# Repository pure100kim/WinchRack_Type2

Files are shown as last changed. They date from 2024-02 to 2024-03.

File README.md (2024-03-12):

# WinchRack_Type2 

# 1. WinchRack_Type2_V1 Release

WinchRack_Type2 V1 for ERCF buffer 

youtube WinchRack_Type2 V1 Testing video : https://www.youtube.com/watch?v=6KahxyvfvtI<br>

ERCF(당근)과 연동하여 테스팅한 유투브 영상입니다.<br>
youtube WinchRack_Type2 V1 Applying ERCF video : https://www.youtube.com/watch?v=UDQim4SroeI

v6cl (방탄쪼끼) is a nice member of the same country and VORON User kakao chat room. <br>
He is adept at design and has helped shortcomings in the multi-color ERCF buffer, for which we are grateful. <br>
Building upon his design, I have received wonderful ideas to modify the structure for improved spatial aspects and easier spool install.

방탄쪼끼님 멋져요!

You can access his original material through the link below.<br>

v6cl WinchRack original Verison github : https://github.com/v6cl/WinchRack/tree/main

v6cl Test youtube video : https://www.youtube.com/shorts/trHfZH3sDRs

# WinchRack Type2

<div align="center">
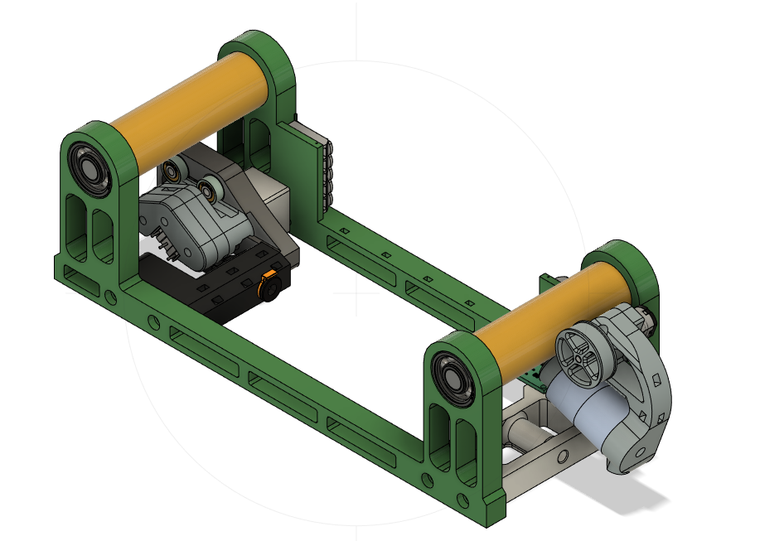
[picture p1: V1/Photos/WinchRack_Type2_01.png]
	<br>
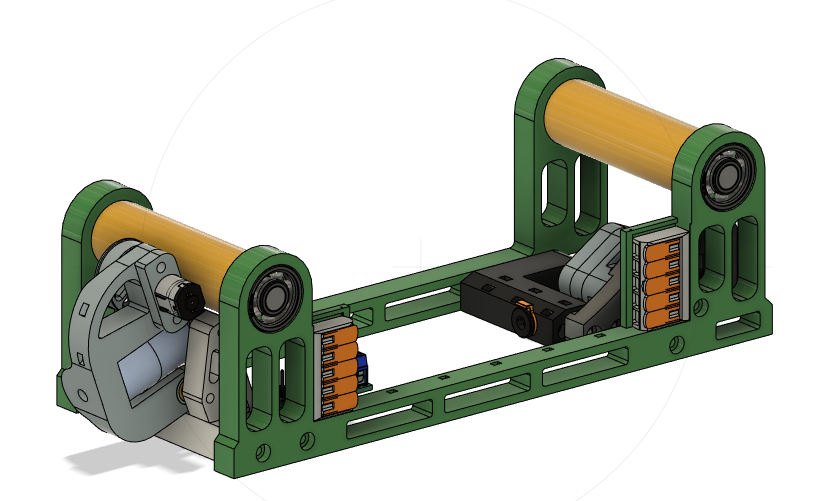
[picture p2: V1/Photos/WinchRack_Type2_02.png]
	<br>
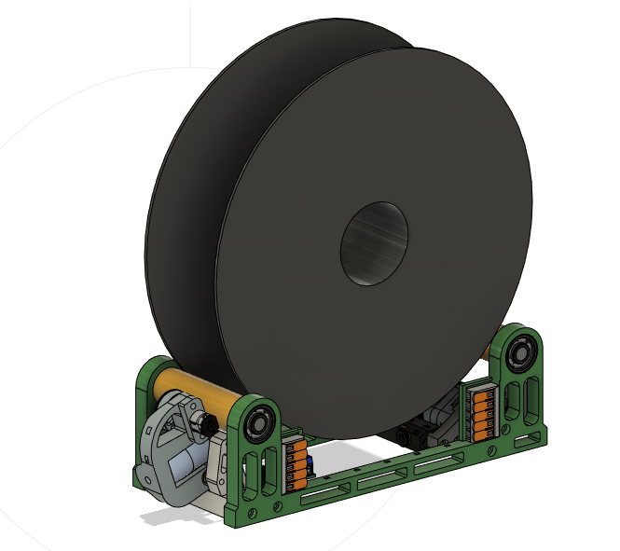
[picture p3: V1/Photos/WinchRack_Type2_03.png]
	<br>
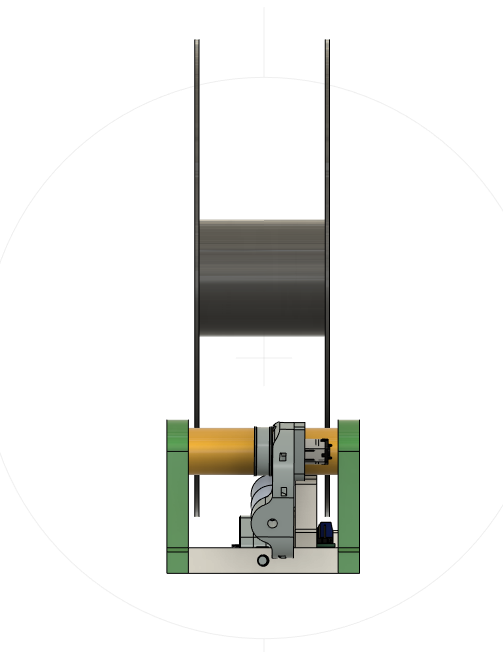
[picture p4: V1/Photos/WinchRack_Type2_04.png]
 	<br>
</div>
<br>

# BOM
Winchrack base component list has been imported as is.<br>

Wago 5pin x 2

(Choose option1) Opto endstop x 1 (https://zrr.kr/ZYrV)

(Choose option2) Opto interrupt x 1 (https://a.aliexpress.com/_oFFfkt0)

n20 gear motor 300 rpm 5v ~ 6v x 1 (https://zrr.kr/33Ta)

ls-p20/15 3kg x 2 (https://zrr.kr/Rqkb)

mosfet switch 1ch x 1 (https://zrr.kr/TrOc)

608zz x 8 (optoion 1 more : you can get 4mm bearing ball 608zz decomposition)

623zz x 8

silicon ring x 1 (https://zrr.kr/E5Dk)

PTFE tube 3x4 or 2x4

m3 insert nut (OD 5mm, L 4mm)

m3 bolts

m4 bolt 15mm x 2 (For ls-p20/15)

m2 self tapping screw 8~10mm x 4

6mm collet for 4mm PTFE Tube x 1 (https://zrr.kr/7WdG)

D2F Micro switch

4mm Bearing ball (608zz including 7 pcs 4mm ball. You can get it decomposition 608zz) 

<br>
<br>
<br>

# Connection Diagram (연결도)
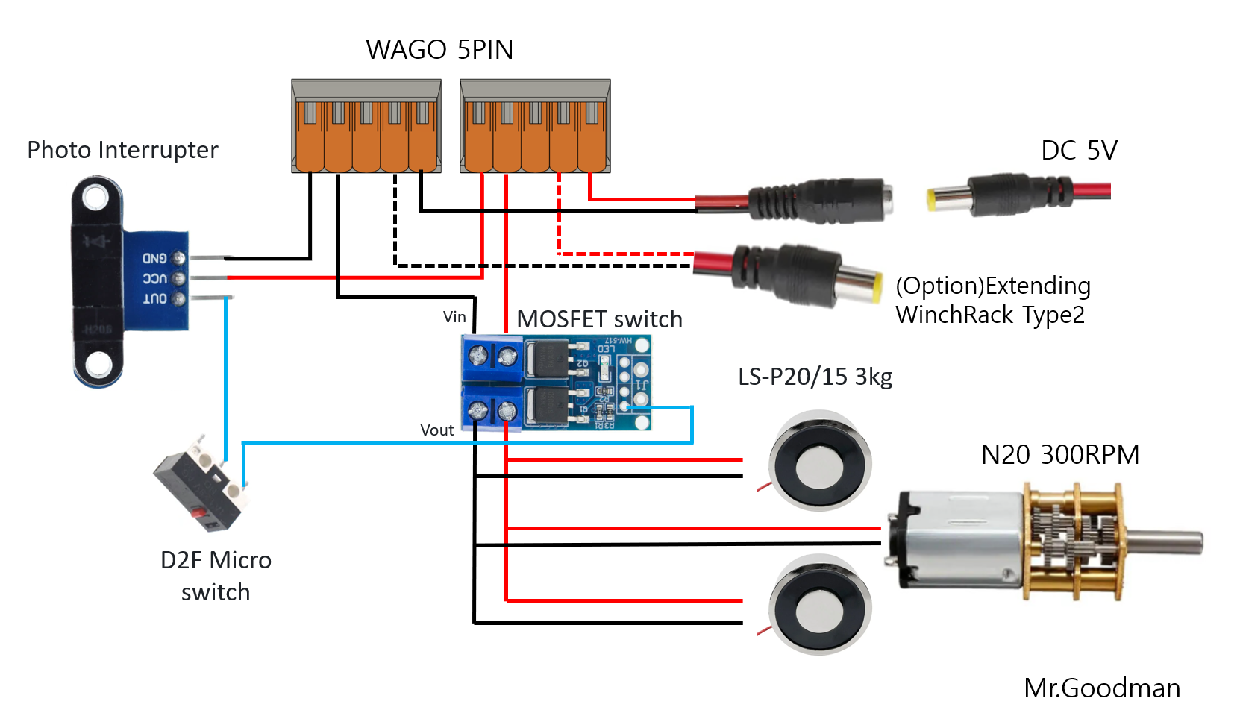
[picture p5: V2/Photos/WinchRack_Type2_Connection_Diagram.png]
<br>

<br>
<br>
<br>
# Assembly precautions
When assembling, make sure to clean the inside of the 608 bearing to ensure smooth rotation when turned.
The bearing should rotate smoothly with minimal friction, at least for several turns.

Due to the friction of the bearing balls, the front and rear rails move, so be sure to assemble the 4mm bearings and switches.
<br>
<br>

# Depend on AccelMotor Revers Assembly motor direction
It is permissible to change the polarity of the power supply to reverse the motor direction, or to relocate the motor while maintaining the polarity marked on the motor as positive (+).
If you changing motor location, use stl file AccelMotor_mag_holder_Frame_Reverse.stl and FrontFoot_Reverse.stl

<br>
<br>
<br>

# 2. WinchRack_Type2_V2 version Release

1. AccelPedal 623zz 고정할때 둥근머리 볼트로 고정해야 합니다.<br>
When fixing AccelPedal 623zz, you should use a rounded head M3 bolt.

2. AccelPedal 조립 후 스풀 롤러와 Accel Roller 고무와 마찰이 잘 되도록 하기 위해<br>
   전자석이 1mm 정도 떨어졌다 붙었다 하게 됩니다.<br>
   최적 위치 조절하면서 볼트를 조여 주세요.<br>
After assembling the AccelPedal, the electromagnet should be positioned about 1mm away and then attached,<br>
allowing for optimal adjustment while tightening the rear bolt to ensure good friction between the spool roller and the Accel Roller rubber.   

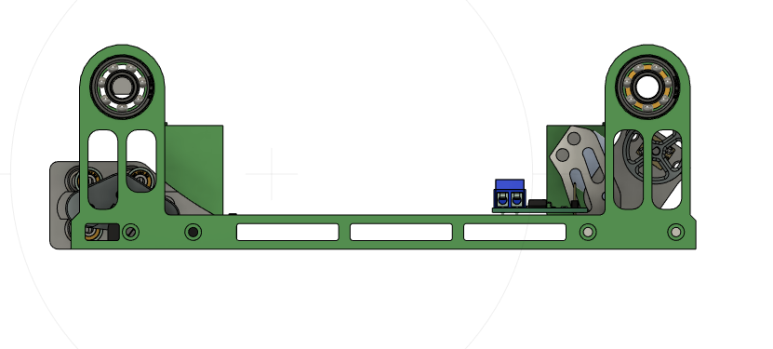
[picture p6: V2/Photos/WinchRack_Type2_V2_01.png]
<br>

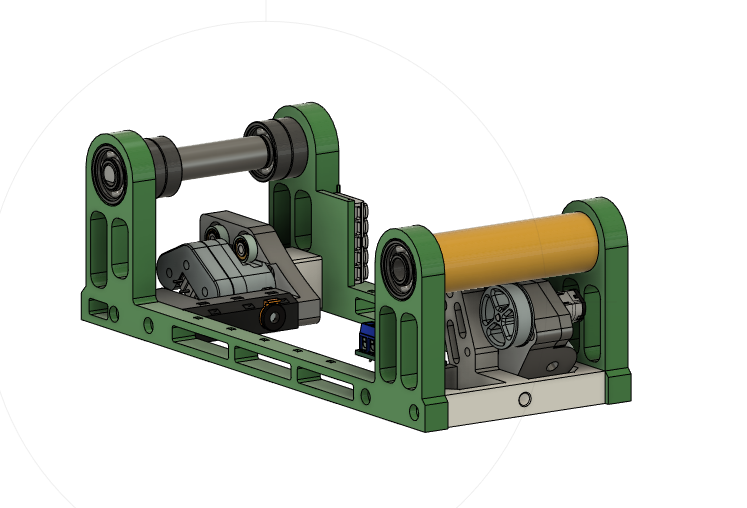
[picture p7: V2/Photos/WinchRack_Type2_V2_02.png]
<br>

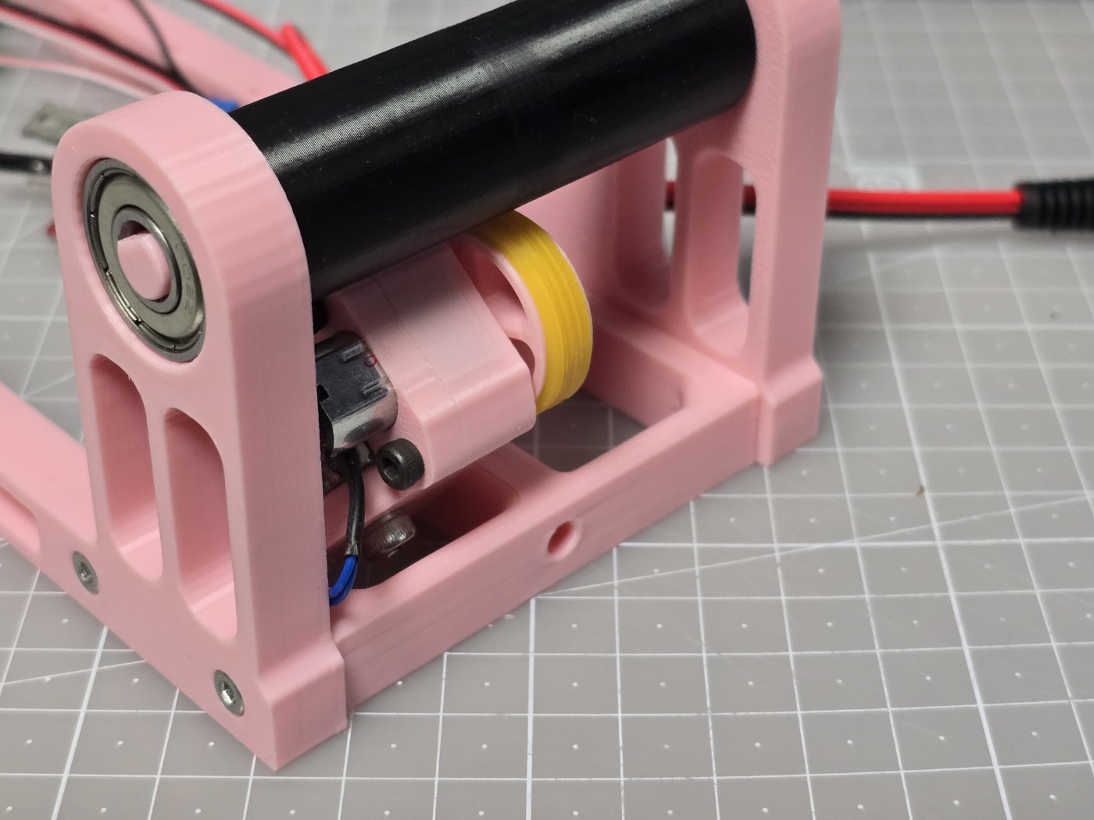
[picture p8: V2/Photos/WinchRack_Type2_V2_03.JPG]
<br>

<br>
<br>
<br>

# 3. WinchRack_Type2 Weight : Filament reamiining Weight version Release

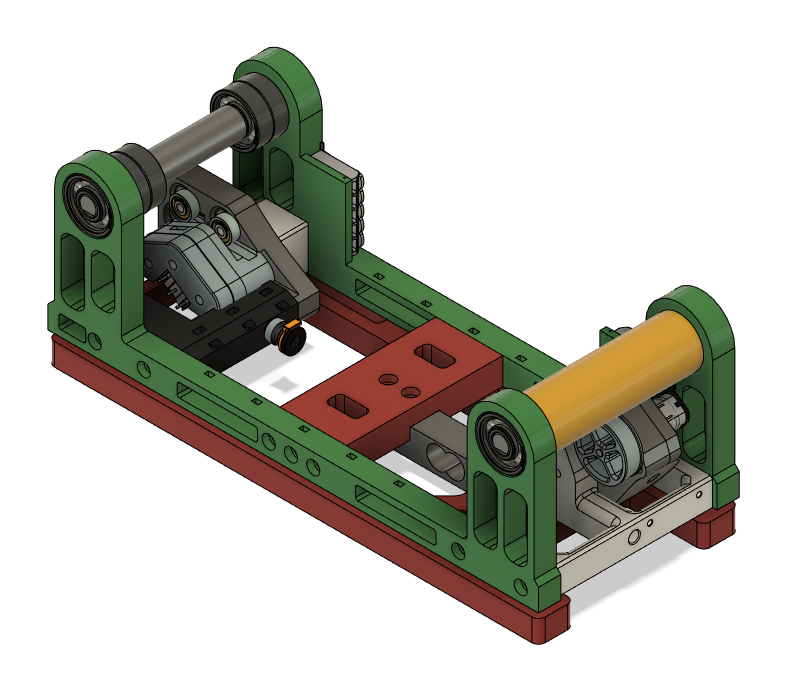
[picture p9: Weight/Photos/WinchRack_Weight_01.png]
<br>

# WinchRack_Type2 Weight Version Add Bom (추가 부품)

1. 5kg 무게 저울 센서 (보드 포함) 1개 <br>
   5kg Loadcell including HX711
2. 아두이노 NANO 1개 <br> 
   Arduino Nano Board <br>
   Recommnad small size board : ESP32-C3    
4. 0.96 inch OLED 12C 버전 1개 <br>
5. M3 insert 6 PCS <br>
6. M4*12mm 4 PCS <br>
7. M3*8mm 6개<br>
8. 기타 전원선<br>

<br>
<br>
<br>

# WinchRack Type2 V3 BelayStlye : Design in progress

<br>
<br>

# History <br>
### 21 Feb 2024 : Changing Modeling base on v6cl WinchdRack <br>
### 22 Feb 2024 : Currently in beta testing. <br>
### 23 Feb 2024
1. File modification for filament switch performance enhancement : SensorDetection_middle_Narrow.stl file.
2. Motor Mount location changing.
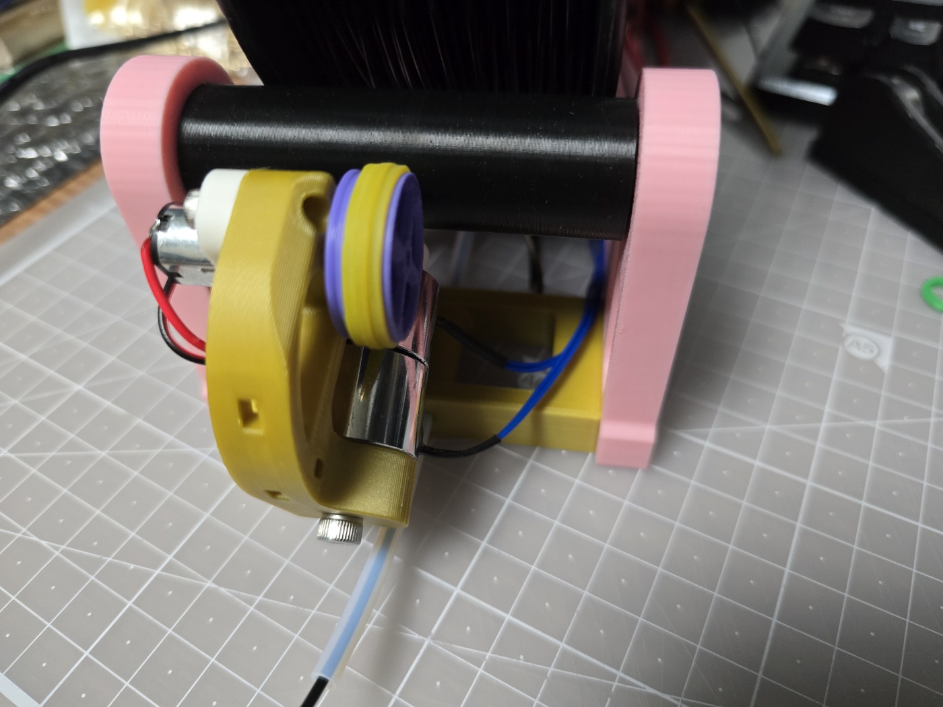
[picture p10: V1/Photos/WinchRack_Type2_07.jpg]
<br>

### 24 Feb 2024<br>
1. Changing Rear Roller 608zz 4pcs instead of printout TPU Roller.
2. Add 2.5mm ~ 3mm space and 41mm pipe. You can adjust gap.
3. Version1 Final Release
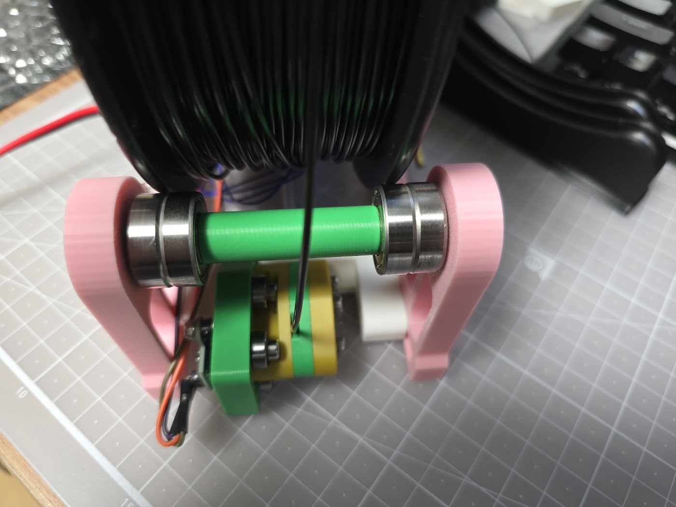
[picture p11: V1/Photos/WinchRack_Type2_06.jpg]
<br>

### 27 Feb 2024<br>
락액락 통에 넣을 수 있는 사이즈로 길이를 줄였습니다.<br>
1. Reduce lenth to 227mm
   
<br>

### 28 Feb 2024<br>
필라멘트 잔여량 측정이 가능하도록 무게 측정하는 버전 개발 진행<br>
1. Spool Weight Beta Testing version Modeling added

<br>

### 29 Feb 2024<br>
테스팅결과 스풀의 무게로 롤러 양쪽이 쳐지는 문제가 발생이 되었습니다.<br>
구조적으로 쳐짐이 발생되지 않도록 설계 보강하였습니다.<br>

1. Design Change to Withstand Spool Weight Load <br>
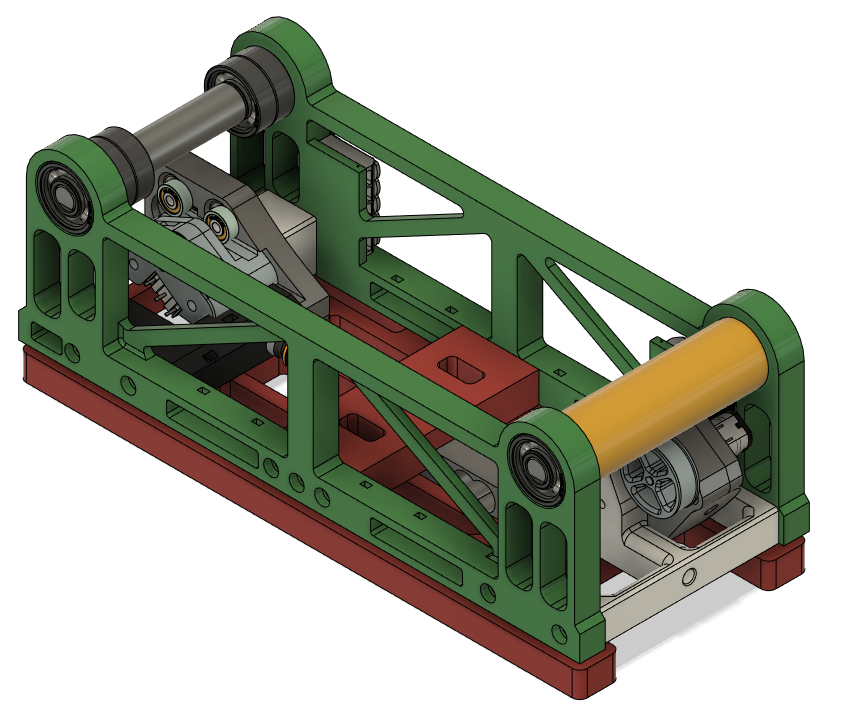
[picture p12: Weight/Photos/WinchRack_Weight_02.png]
<br>

### 01 Mar 2024<br>
1. Filament Remaing Weight arduino coding verify complted <br>
2. Relase Measure Filament remaing weight <br>
3. Writing Connection Diagram <br>
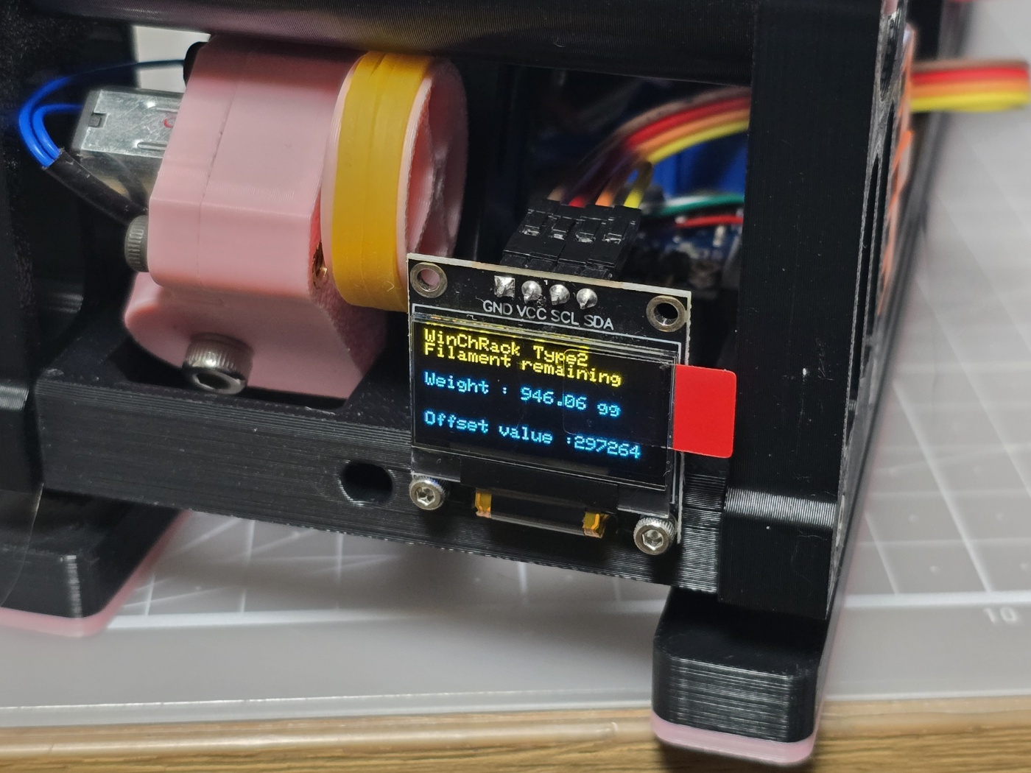
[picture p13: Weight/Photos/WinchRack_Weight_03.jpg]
<br>

### 12 Mar 2024<br>
1. WinchRack V3 is redesigning the sensor rail to be simpler and reduce bearing parts.

감사합니다.

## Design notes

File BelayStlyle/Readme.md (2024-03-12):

The design of the sensor rail method is being changed to another style.<br>
Many bearings will be removed.

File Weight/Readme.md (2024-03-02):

# WinchRack_Type2 V3 Weight scale Version Relase

Youtube video : https://youtu.be/h_89rF7SB6s?si=DVgz_AW4CbowRDjg

<br>

1. AccelPedal 623zz 고정할때 둥근머리 볼트로 고정해야 합니다.<br>
When fixing AccelPedal 623zz, you should use a rounded head M3 bolt.

2. AccelPedal 조립 후 스풀 롤러와 Accel Roller 고무와 마찰이 잘 되도록 하기 위해<br>
   전자석이 1mm 정도 떨어졌다 붙었다 하게 됩니다.<br>
   최적 위치 조절하면서 볼트를 조여 주세요.<br>
After assembling the AccelPedal, the electromagnet should be positioned about 1mm away and then attached,<br>
allowing for optimal adjustment while tightening the rear bolt to ensure good friction between the spool roller and the Accel Roller rubber.   

<br>

<br>

<br>

# Add Bom (추가 부품)

1. 5kg 무게 저울 센서 (보드 포함) 1개 <br>
   5kg Loadcell including HX711
2. 아두이노 NANO 1개 <br>
   Arduino Nano Board
3. 0.96 inch OLED 12C 버전 1개 <br>
4. M3 insert 6 PCS <br>
5. M4*12mm 4 PCS <br>
6. M3*8mm 6개<br>
7. M3*8mm 1개(둥근머리) <br>
8. 기타 전원선<br>

<br>

<br>

# Loadcell Connection Diagram
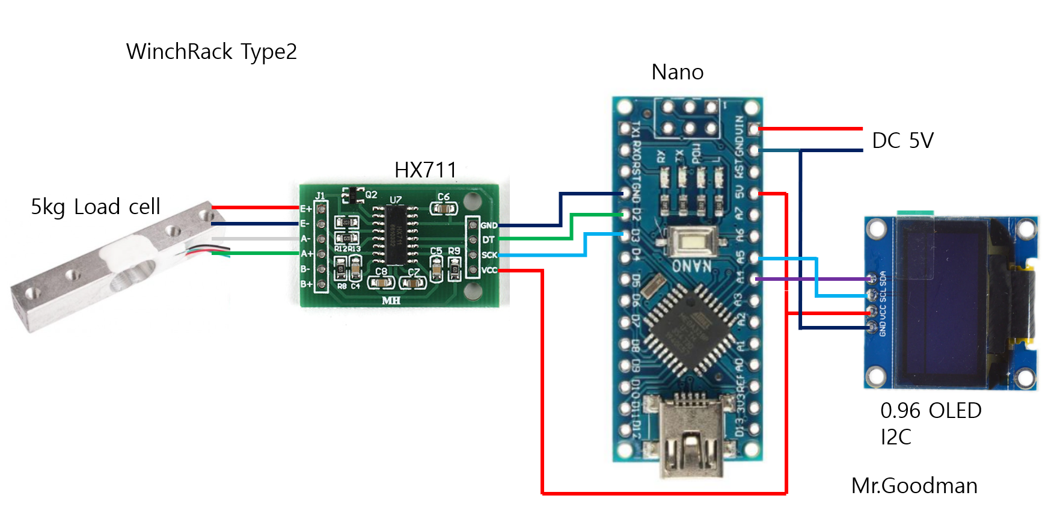
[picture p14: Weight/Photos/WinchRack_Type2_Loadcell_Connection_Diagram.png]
<br>

# History

29 Feb 2024 <br>
Design Change to Withstand Spool Weight Load <br>

01 Mar 2024
1. LoadCell Arduino Nano Coding complted <br>
2. Writging Connection Diagram <br>

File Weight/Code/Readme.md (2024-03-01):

아두이노로 필라멘트 잔량을 표기하는 아두이노 코드입니다.

# 적용 순서

1. WinchRack_offset_measure.ino 코드 적용 후 offset값 측정 및 기입 <br>
2. 빈 스풀 무게 실측값 측정<br>
3. WinchRack_Filament_remaining_Weight.ino 코드에 offset값과 빈스풀 무게 실측값 기입<br>
4. 코드 적용<br>

위에 1번과 2번에서 빈스풀을 올린 후 offset값을 측정하여도 무방하긴합니다.<br>
코드 약간 수정하면 되긴합니다.

감사합니다.

# Application Sequence

1. Apply the WinchRack_offset_measure.ino code and measure the offset value, then record it.  <br>
2. Measure the actual weight of the empty spool. <br>
3. Enter the offset value and the measured weight of the empty spool into the WinchRack_Filament_remaining_Weight.ino code. <br>
4. Apply the modified code. <br>

It is acceptable to measure the offset value after winding the empty spool in steps 1 and 2 above.
Minor modifications to the code may be necessary.

Thankyou~ :D

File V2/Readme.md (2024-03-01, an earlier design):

# WinchRack_Type2_V2

락앤락 통에 넣을 수 있도록 사이즈를 줄인 버전입니다.

전체 사이즈 : 가로 227mm x 폭 90mm x 높이 220mm (스풀 지름 200mm 일때 기준)

# Assembly precautions
When assembling, make sure to clean the inside of the 608 bearing to ensure smooth rotation when turned.
The bearing should rotate smoothly with minimal friction, at least for several turns.

Due to the friction of the bearing balls, the front and rear rails move, so be sure to assemble the 4mm bearings and switches.
<br>
<br>

1. AccelPedal 623zz 고정할때 둥근머리 볼트로 고정해야 합니다.<br>
When fixing AccelPedal 623zz, you should use a rounded head M3 bolt.

2. AccelPedal 조립 후 스풀 롤러와 Accel Roller 고무와 마찰이 잘 되도록 하기 위해<br>
   전자석이 1mm 정도 떨어졌다 붙었다 하게 됩니다.<br>
   최적 위치 조절하면서 볼트를 조여 주세요.<br>
After assembling the AccelPedal, the electromagnet should be positioned about 1mm away and then attached,<br>
allowing for optimal adjustment while tightening the rear bolt to ensure good friction between the spool roller and the Accel Roller rubber.

3. 만약 그래도 Accel Roller와 스풀 롤러간 마찰이 잘 안된다고 하면 스풀 롤러 지름 22mm에서 23mm로 CAD수정하여 출력해보세요.
   스풀 롤러는 외경 22mm, 내경 8mm, 길이 69mm 입니다.

<br>

<br>
<br>
<br>

둥근머리 M3*10mm로 먼저 조립한 후 전자석을 조립합니다.<br>

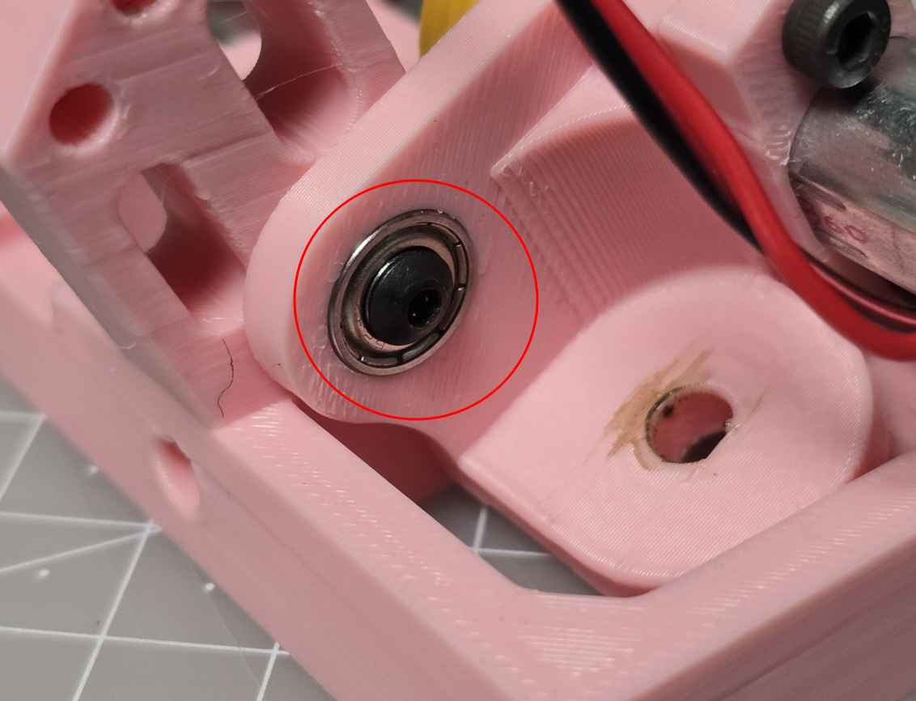
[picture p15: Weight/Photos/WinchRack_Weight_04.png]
<br>

<br>

<br>
<br>
<br>

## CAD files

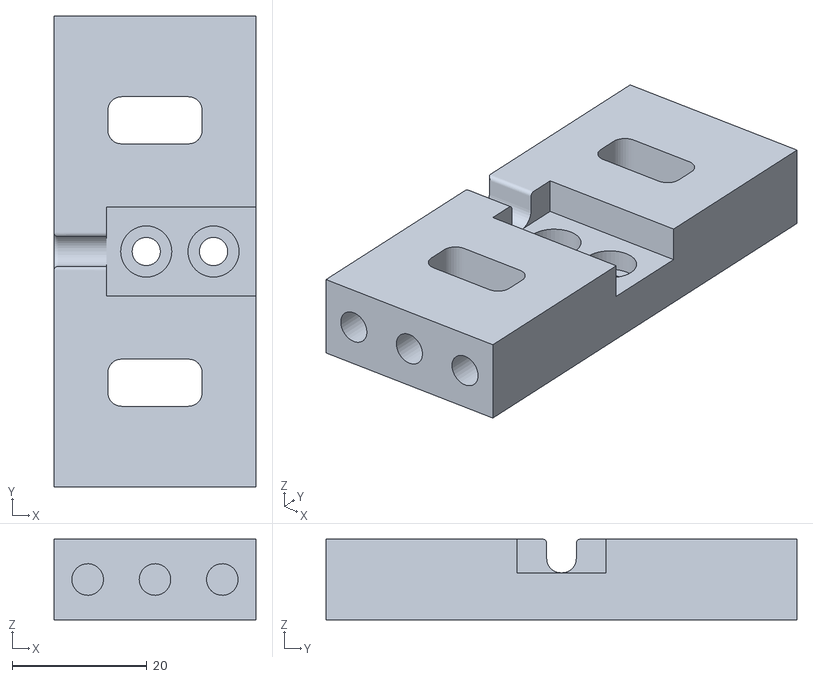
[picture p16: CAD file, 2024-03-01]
Weight/STLs/WeightBase/Weight_Holder.stl
30.0 x 70.0 x 12.0

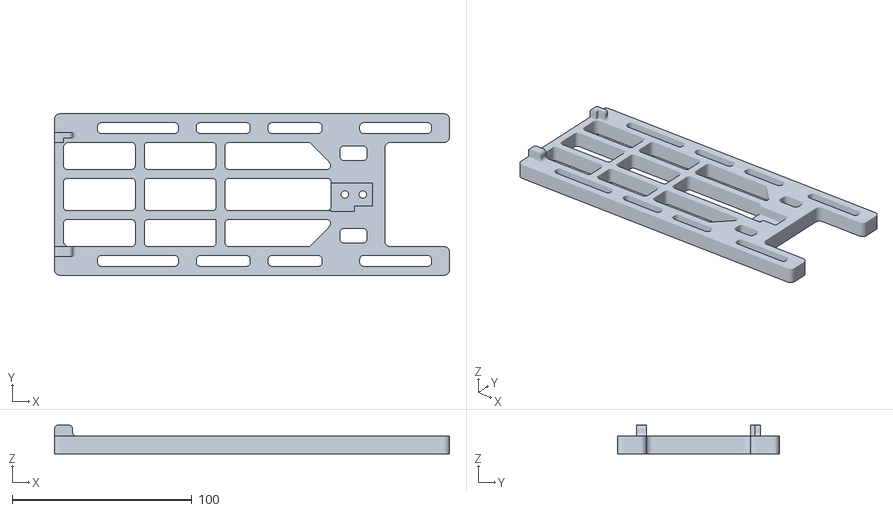
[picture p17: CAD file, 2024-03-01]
Weight/STLs/WeightBase/Weight_base.stl
220.0 x 90.0 x 16.0

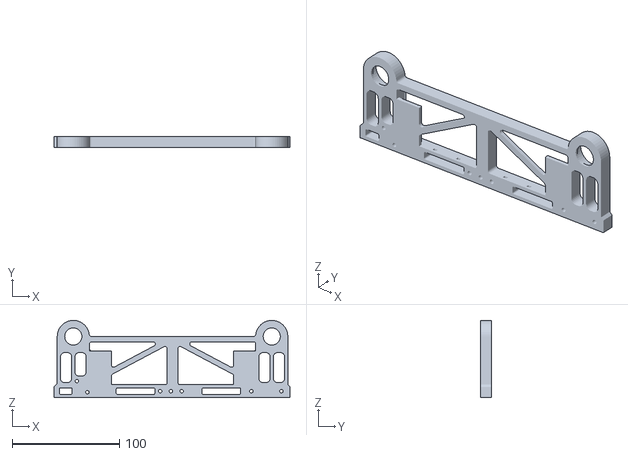
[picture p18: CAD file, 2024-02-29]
Weight/STLs/WeightBase/Base_Right_Weight.stl
220.0 x 10.0 x 72.0

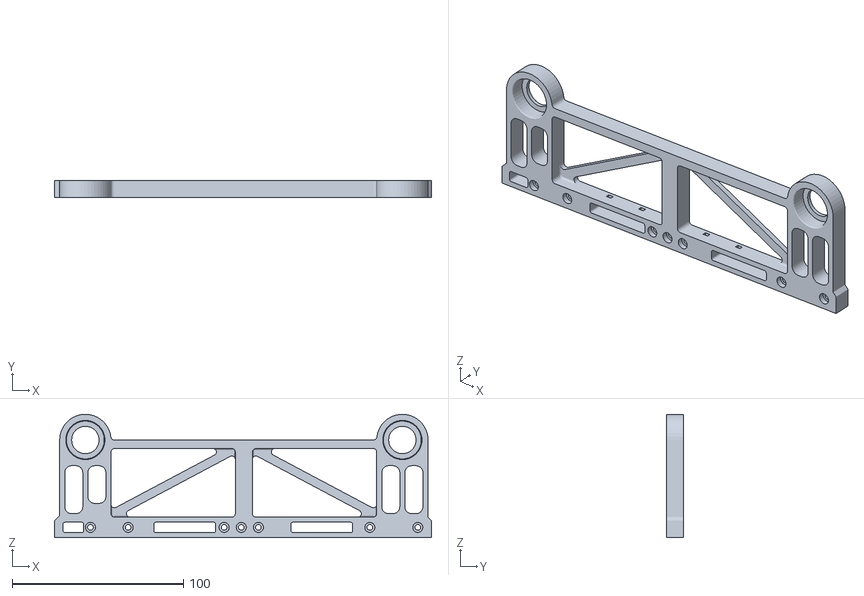
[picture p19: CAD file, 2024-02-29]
Weight/STLs/WeightBase/Base_Left_Weight.stl
220.0 x 10.0 x 72.0

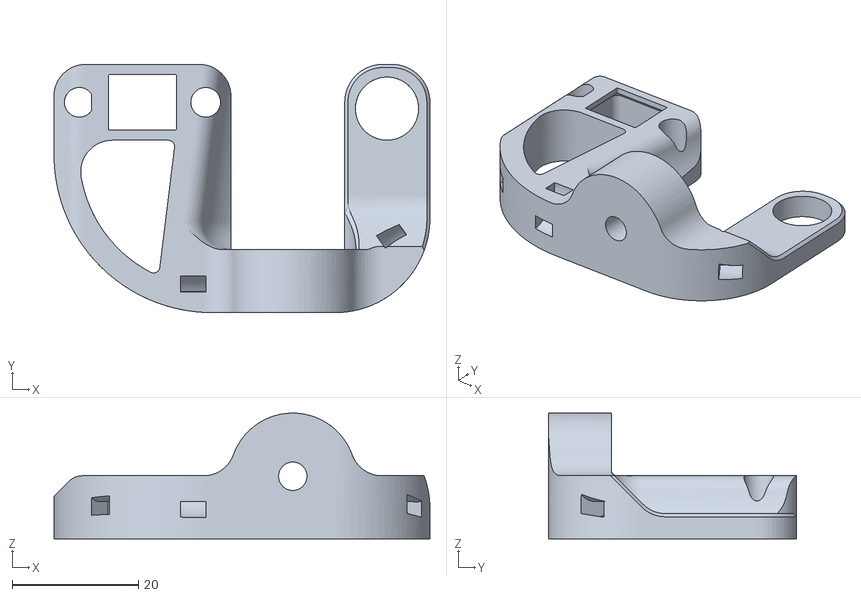
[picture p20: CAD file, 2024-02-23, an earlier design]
V1/STLs/AccelMotor/AccelMotor_mag_holder_Frame_Reverse.stl
59.5 x 39.3 x 19.9

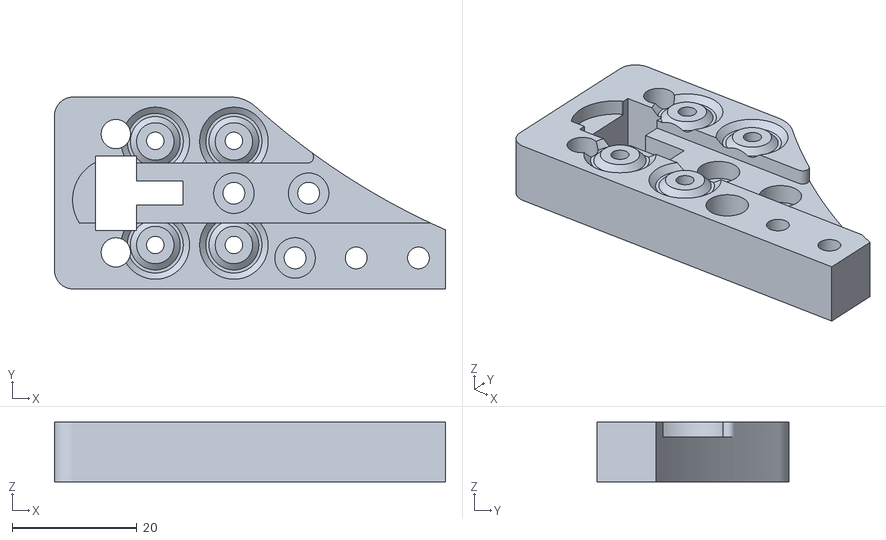
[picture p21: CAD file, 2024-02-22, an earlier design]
V1/STLs/SensorDetection/BufferRail.stl
62.8 x 30.8 x 9.58

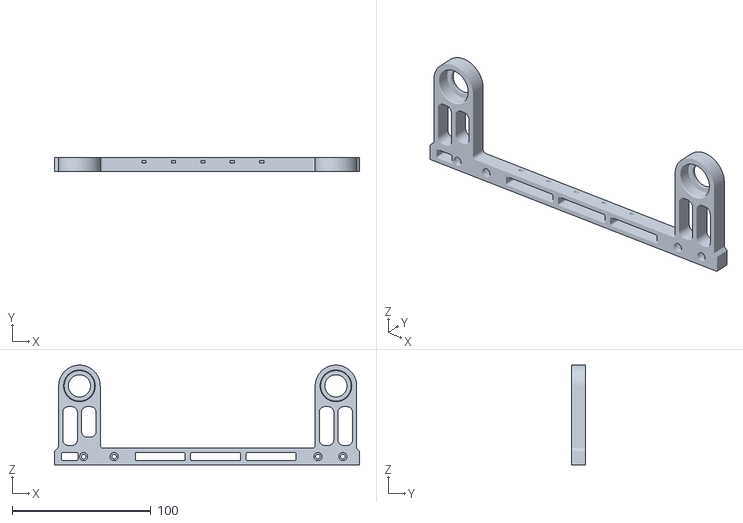
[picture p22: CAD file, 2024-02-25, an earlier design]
V1/STLs/SpoolBase/Base_Left.stl
220.0 x 10.0 x 72.0

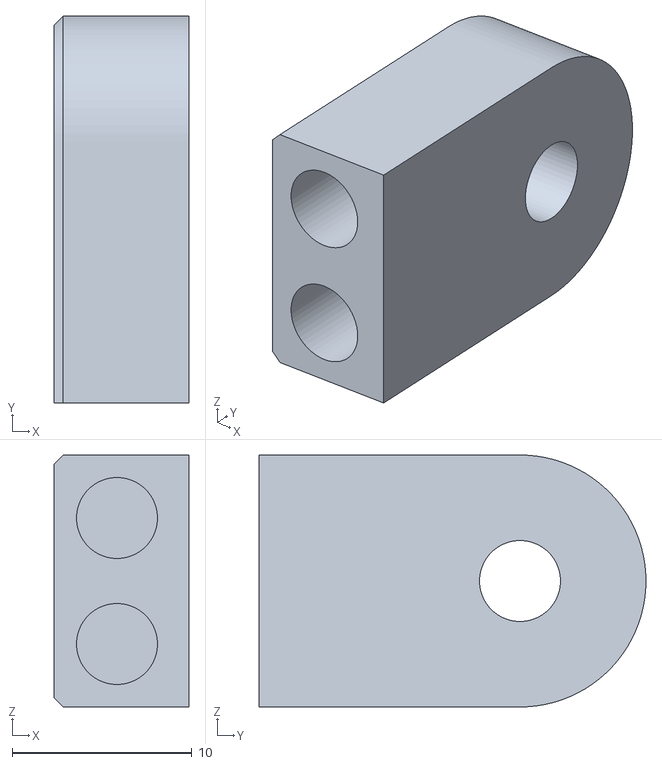
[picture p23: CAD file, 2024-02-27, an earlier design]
V2/STLs/AccelMotor/AccelPedal_mag_holder.stl
7.50 x 21.5 x 14.0

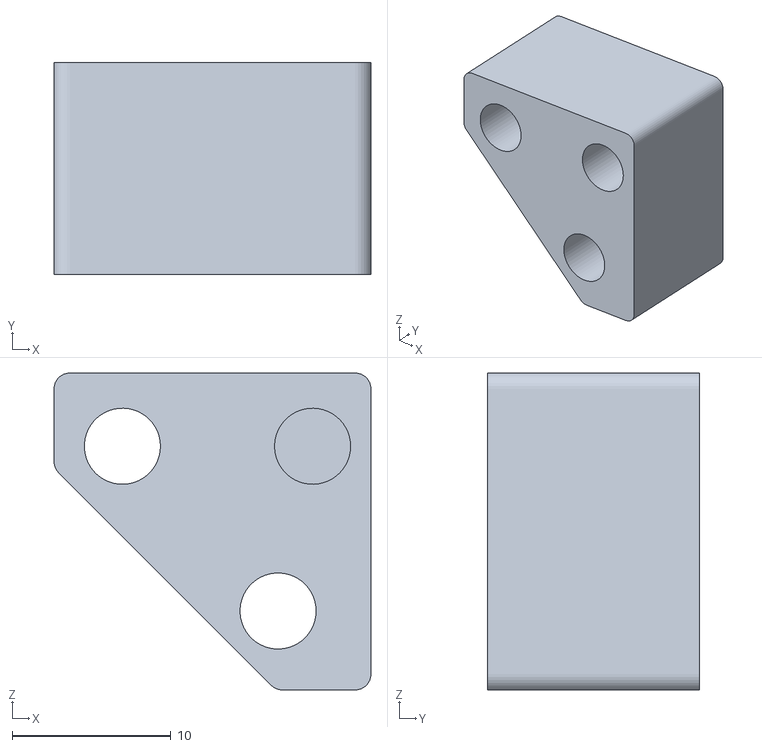
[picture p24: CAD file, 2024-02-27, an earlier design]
V2/STLs/SensorDetection/SensorDetection_sensor_basemount.stl
20.0 x 13.3 x 20.0

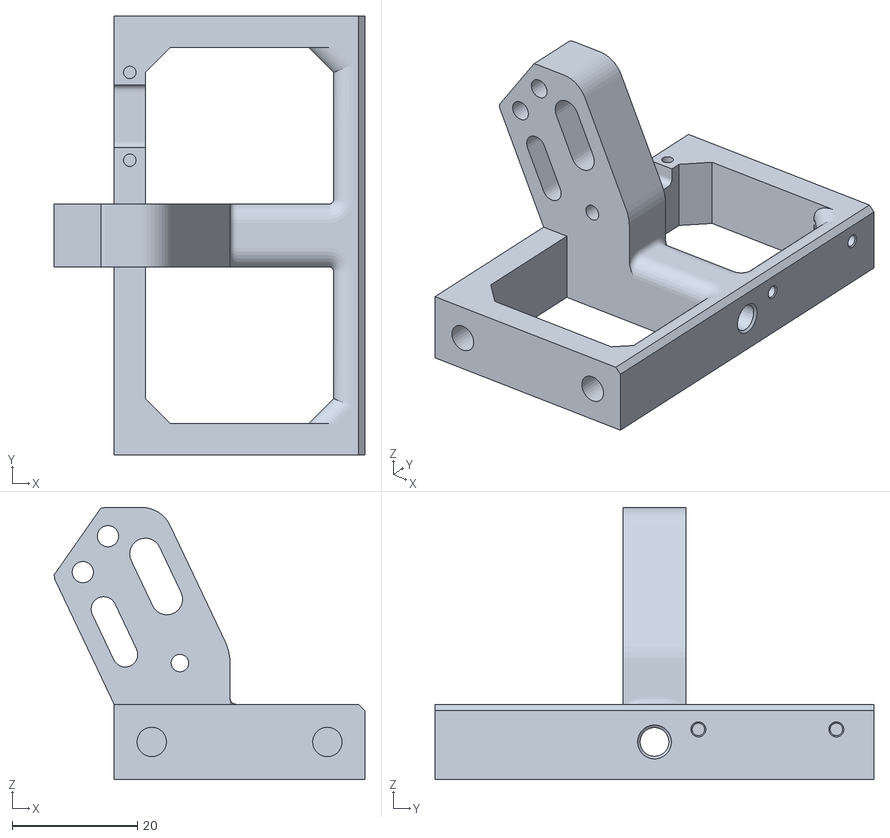
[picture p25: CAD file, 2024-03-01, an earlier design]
V2/STLs/SpoolBase/Front Base_Accel_Pedal_Mount.stl
49.6 x 70.0 x 43.4

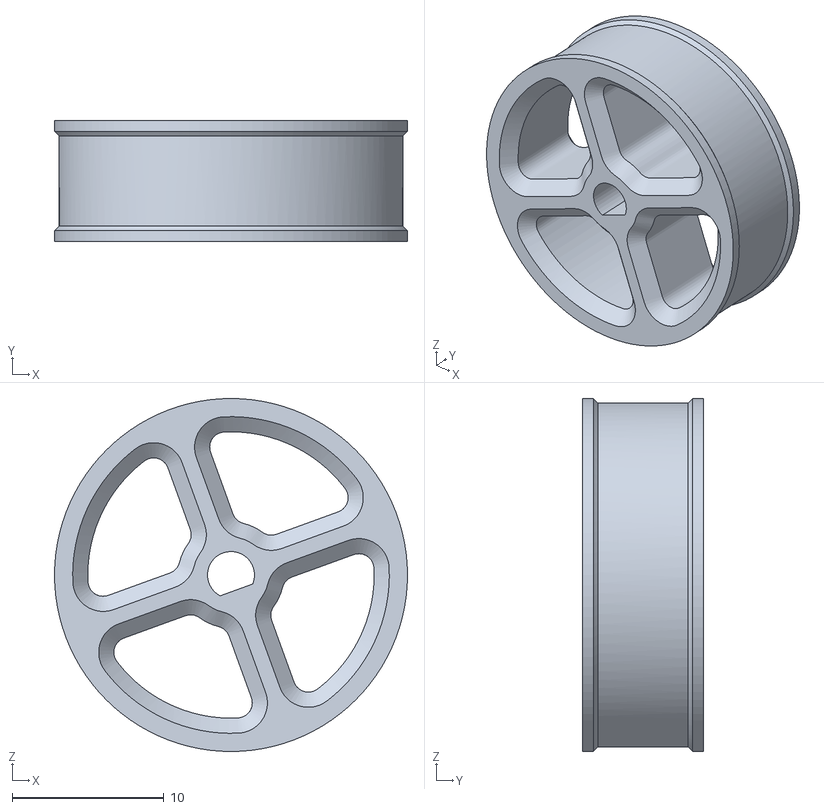
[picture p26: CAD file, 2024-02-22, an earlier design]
V1/STLs/AccelMotor/AccelMotor_mag_Roller.stl
23.3 x 8.00 x 23.3

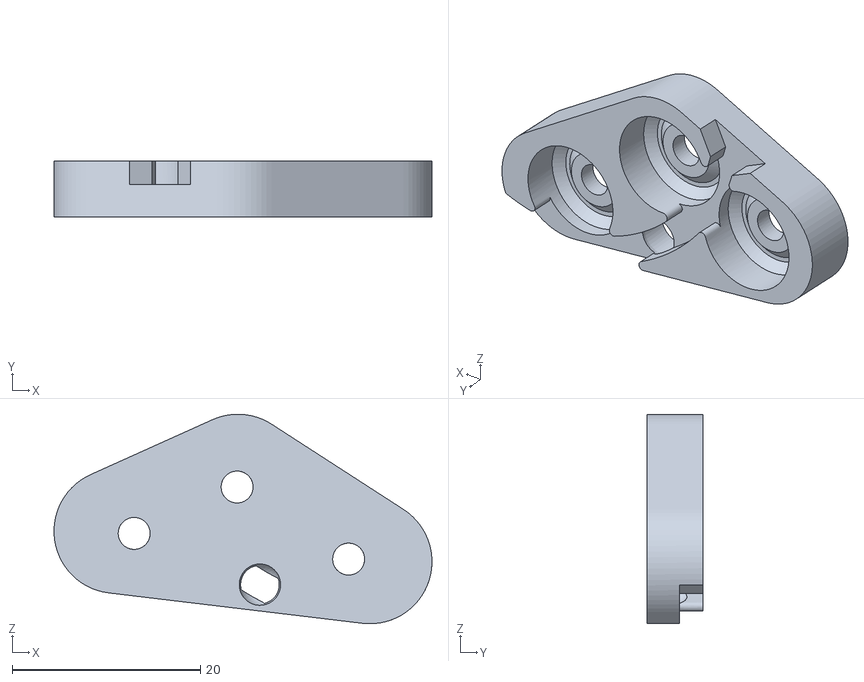
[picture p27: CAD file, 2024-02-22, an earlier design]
V1/STLs/SensorDetection/SensorDetection_middle.stl
40.2 x 5.91 x 22.3

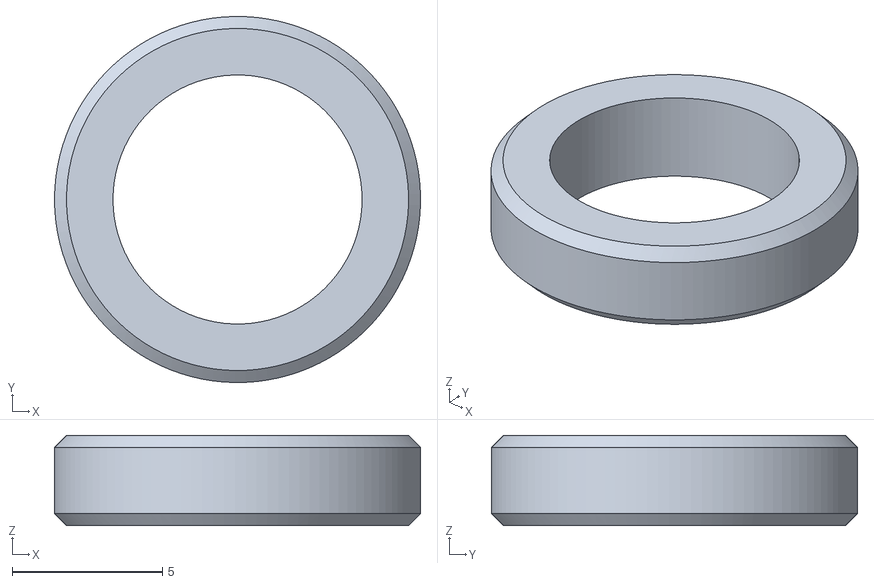
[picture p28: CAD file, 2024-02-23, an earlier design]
V1/STLs/SpoolBase/3mm_space.stl
12.2 x 12.2 x 3.00

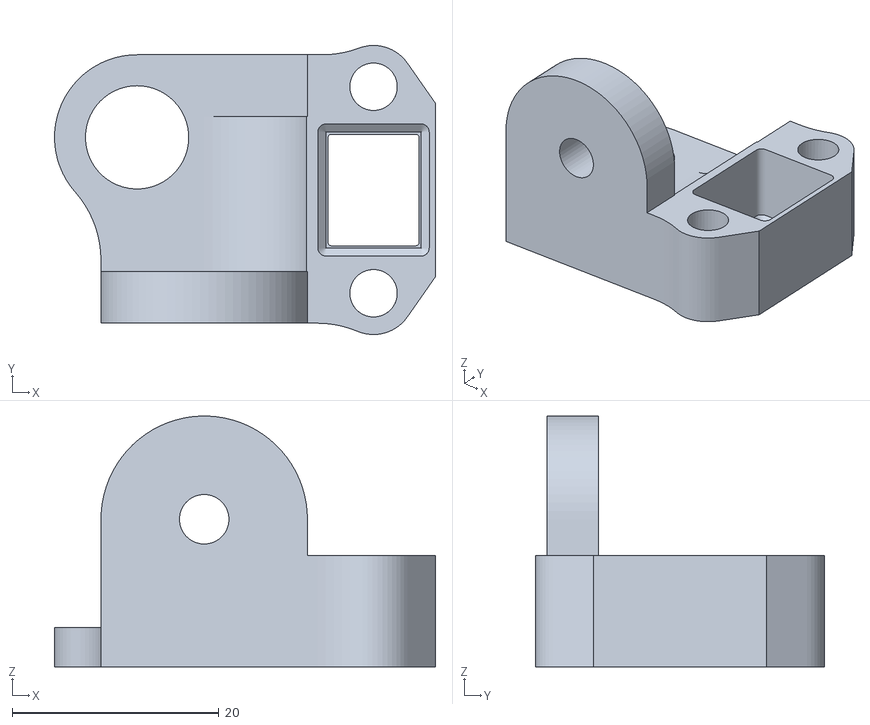
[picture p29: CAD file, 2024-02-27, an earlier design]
V2/STLs/AccelMotor/AccelPedal_mag_Body_Left.stl
36.9 x 28.0 x 24.3

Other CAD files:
V1/CAD/WinchRack_windre_Type2.step
V2/STLs/SensorDetection/SensorDetection_middle_Narrow.stl
V1/STLs/AccelMotor/AccelMotor_motor_holder.stl
V1/STLs/AccelMotor/AccelMotor_mag_holder.stl
V1/STLs/SpoolBase/Base_Right.stl
V1/STLs/SpoolBase/BufferBase_mount.stl
V1/STLs/SpoolBase/FrontFoot_Reverse.stl
V1/STLs/SpoolBase/Roller1_TPU.stl
V1/STLs/SpoolBase/Shaft1.stl
V1/STLs/SpoolBase/Shaft2.stl
V2/STLs/AccelMotor/AccelPedal_Motor_holder.stl
V2/STLs/AccelMotor/AccelPedal_Roller.stl
V2/STLs/SensorDetection/SensorDetection_Buffer_Rail_mcmcu.stl
V2/STLs/SensorDetection/SensorDetection_Photo_senseKey.stl
V2/STLs/SensorDetection/SensorDetection_Rail.stl
V2/STLs/SensorDetection/SensorDetection_Switch_mount.stl
V2/STLs/SpoolBase/2.5mm_space x 4.stl
V2/STLs/SpoolBase/41mm_pipe.stl
V2/STLs/SpoolBase/Base_Left_V2.stl
V2/STLs/SpoolBase/Base_Right_V2.stl
V2/STLs/SpoolBase/Roller1_TPU.stl
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

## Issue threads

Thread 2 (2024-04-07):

STL missing for BufferBaseMount in stl folders.

robandwend, 2024-04-07:
Minor issue - I note that the STL folder is missing the required stl for "BufferBaseMount v1" (I've extracted from the f3d - so not really a problem).

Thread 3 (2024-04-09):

STL missing in V2 for bufferrail

robandwend, 2024-04-09:
The BufferRail stl in V2 does not include the version called 'bufferrail.stl' that is found in the V1 version which is needed when using the opto-isolator option (rather than the opto interrupter).

Possibly the V2 is designed to only use the opto-isolator, however this isn't clear from the V2 BOM.

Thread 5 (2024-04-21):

doesn't work correctly

Oasis1981, 2024-04-21:
builded.

the magnet position it's a pain
the alternative sensor doesn't work, active the rewinder when you pull the filament, not when you push

the bearing system for move the filament entrance it's very misteious.
the bearings inside the filament entrance are too nearly and the filament don't pass.

needs detailed instruction for a correct build

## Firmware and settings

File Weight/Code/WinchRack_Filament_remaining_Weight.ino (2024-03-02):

#include "HX711.h"
#include <Wire.h>
#include <SSD1306Ascii.h> // i2C OLED
#include <SSD1306AsciiWire.h> // i2C OLED

// I2C pins:
// Arduino: SDA: A4 SCL: A5

// HX711 회로 연결
#define LOADCELL_DOUT_PIN 2 //DT
#define LOADCELL_SCK_PIN  3 //SCK

// loadcellvalue 설정
float loadcellValue = 372.0; // 5kg loadcell에 대한 값을 사용

// 측정한 offset값 및 빈 스풀의 무게 적용
float offsetValue = 297264; // 측정한 offset 적용시 무게 -0.81g
float emptySpoolWeight = 250.0; // 빈 스풀 측정한 무게 250g 기입


HX711 scale;
SSD1306AsciiWire oled;

void setup() {
  Serial.begin(115200);

  // 로드셀 HX711 보드 핀 설정
  scale.begin(LOADCELL_DOUT_PIN, LOADCELL_SCK_PIN);

  // OLED 초기화 및 "WinchRack Type2 scale" 표시
  Wire.begin();
  oled.begin(&Adafruit128x64, 0x3C);

  oled.setFont(Adafruit5x7);
  oled.clear();
  oled.println("WinchRack Type2");
  oled.println("Filament remaining");
  oled.println("");
  oled.println("Created by Mr.Goodman");

  // 부팅 후 잠시 대기 (2초)
  delay(2000);

  // offset, scale 셋팅
  scale.set_offset(offsetValue);
  scale.set_scale(loadcellValue); 

  // 설정된 오프셋 및 스케일 값 확인
  oled.print("Offset value :\t");
  oled.println(scale.get_offset());
  oled.print("Scale value :\t");
  oled.println(scale.get_scale());


  // 3초 대기 후 OLED 클리어
  delay(3000);
  oled.clear();

  // 무게 안내문자 표시
  oled.println("WinchRack Type2");
  oled.println("Filament remaining");
  
}

void loop() {
  float value;
  float Weight;

  // 무게 측정값 (7회 측정 평균값) 
  value = scale.get_units(7);
  
 // 필라멘트 잔량  계산 및 표기
  Weight = value - emptySpoolWeight;
  oled.setCursor(0, 3);
  oled.print("Weight : ");
  oled.print(Weight);
  oled.println(" g");

 //현재 적용된 스케일값 표기
  oled.setCursor(0, 6);
  oled.print("Offset value :\t");
  oled.println(scale.get_offset());

  delay(1000);

}
